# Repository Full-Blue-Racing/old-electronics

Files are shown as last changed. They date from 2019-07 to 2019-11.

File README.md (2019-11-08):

# FBR20-Electronics

This repo houses all the code the car needs to run, separated into steering 
wheel, telemetry, and CAN bus files.

# Git Gud

[Git Crash Course](https://rogerdudler.github.io/git-guide/)

[Gitlab SSH setup](https://docs.gitlab.com/ee/ssh/)

Git can be separated into remote and local repository (repo), how it works is 
that you can *clone* a repo to your local machine, *add* files you would like 
git to track, *commit* your changes to your local branch, *pull* changes by 
others from the remote repo, and *push* your own local changes. Locally git can 
be separated into three areas:

```Untracked files -> tracked files -> staging area```

Untracked files are usually not part of the project and will not be added to the
repo. Tracked files are project files, and files in here will have status shown 
(i.e. new file/changed/renamed...). The staging area is files that are ready to 
be *committed*, and tracked files needs to be added by ```git add```.

These are the only commands I would recommend using on the command line/IDE, 
for more complex commands (such as creating pull requests for merging branches) 
use the web interface. 

![Image of Git Workflow](https://hackernoon.com/hn-images/1*mQdKYVN0nl-NvTw6MOSkWA.png)

# Best Practices

### No spaces in file names or folder names please

**No direct pushing/committing on the master branch**

1. Use branches

Each of the following tasks are on a separate 
branch, please work on the branch relevant to your task. If multiple people are 
on the same branch please make sub-branches from the main task branch 

*e.g.* 
```
steering-wheel -> steering-wheel-warninglights
               -> steering-wheel-RPM-lights
```

We will merge them into the main steering-wheel branch when you make a merge 
request to the task branch.

2. Micro-commit

Commit every time you've implemented a feature - it allows easy rollback to 
previous version without too much code loss if things go wrong (and they *WILL* 
go wrong).

3. Handy commands

```git config --global user.name <display name>``` - sets your name on your commits to the repo

```git clone <path/to/directory>``` - clones a local copy of the repo to your
machine so you can make changes.

```git pull origin <name of branch>``` - pulls any changes others have 
published on the remote branch of the said name since your last update/ initial 
clone

```git add <file to be added>``` - adds file to the staging area to be included 
in the next commit.

```git commit -m "Commit message here"``` - commits file to the local branch 
with the commit message - please make the commit message meaningful so it is 
easier to backtrack (**Not** ```Add new file```) 

```git push origin <name of branch>``` - push your local commits to the remote 
repo on the named branch. Note that on the first push git may require you to 
set the upstream branch with ```git branch --set-upstream-to <name of head branch>```

```git remote update origin --prune``` - updates branches and removes merged branches 
on your local machine.

# Tasks

Each function to be made are described in respective folders' ```README```,
please edit the ```README``` with your name if you are currently working on the 
task, and remove it if not. If someone is already working on one and you want 
to join, contact them and see if you can help before writing your own code. 
Otherwise just write your name down and contact me (Will) for any 
questions/purchasing.

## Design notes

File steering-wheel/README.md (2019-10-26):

# Steering Wheel LEDs: Ashley & Antonis?

On the steering wheel we have rpm LEDs and indicator LEDs, previously
they were fixed colour LEDs and each one had its own pin on the arduino to 
drive it. This year we want to switch to using WS2812B LEDs (you can find a 
better/ alternative solutions, these are just common) They are RGB LEDs that
are controlled by clocking information through them in series. You can buy 
them in a strip for the purposes of developing them into code.
    
[Link to LED Datasheet](https://cdn-shop.adafruit.com/datasheets/WS2812B.pdf)
    
## Function Requirements:
    
1. We want 19 display LEDs in series. The first and last two are for
   warning lights. The central 15 are for rpm lights
   (see [https://www.youtube.com/watch?v=u5kZjg_sJdg])
  
2. Two variables are passed to the function:
    -rpm (float(can be integer) - revs per minute of engine)
    -clt (float - coolant temperature)
    
3. Warning lights (clt value):
    - below 35 C - LEDs solid blue
    - Between 35 C and 100 C - LEDs off
    - between 100C and 107 C - LEDs solid red
    - Above 107 C - LEDs flashing red
    - Values are rough. Do some research to get more accurate
      information and link your sources. Contact me for engine 
      details

4. RPM lights (rpm value):
    - (left to right) 5 Green, 5 Red, 5 Blue
    - Threshold for each to turn on is a design choice you have to make 
      (do some research and produce a document as this scores points in 
      design presentation) Jonathan Collins is one of the best racers
      in Cambridge so speak to him if you want an idea.
    - Above 12500 ALL the LEDs flash blue (note do this via interrupts, 
      never use delays if possible)

# Steering Wheel Screen: (Insert Name 1 & Name 2 & Name 3 here)

previously we used a screen driven directly via an arduino nano. The problem
was that the arduino was 8-Bit so this meant it lacked the speed to update the
screen smoothly enough to do graphics (could only do text).

This means we have switched to using a Nextion screen:
[Link to Nextion Webside](https://nextion.itead.cc/)

These are seperate microprocessor/screen units that operate at 32-bit. Allowing
graphical displays. They work by communicating via serial to an arduino in the 
steering wheel that is pulling data off the CAN bus.

## Functional Requirements:

1. Decide on which Model to use. There are multiple options so take a look
   at each of the different series and document the option you went for. In 
   terms of size to choose, last year we went with a 3.5" screen and I can
   send photos/CAD of that to give you an idea of size relative to the steering
   wheel. We are going to be reusing the same shape of the centre of the
   wheel so a step down to the 3.2" screen is an idea to play with. Best thing
   to do is play around with CAD and see what will fit with the extra LEDs that
   are going to be at the side of the screen (look at an f1 steering wheel)

2. One of the buttons on the steering wheel will be used to toggle through the
   different screen display modes:
    - Driver Mode
    - Data Mode
    - Standby Mode

3. Keep in mind visibility in the sun and the fact the driver is shaken
   around a lot

4. Driver Mode:
    - Contains a central RPM dial similar to that in cars
    - Clear temperature readoff for clt (coolant temp)
    - Keep in mind the steering wheel tilts when turned when designing
      graphics
    - Display showing gear that you are in (bug me to add this to the car)
    - Other parameters may be added

5. Data Mode:
    - Display all the datafields received over CAN bus in a clear format
    - Might need to display over multiple screens but that is fine

6. Standby Mode:
    - Simply display an image on the screen, if possible a GIF or most desirably
      a Video

# Steering Wheel PCB: (Insert name here)

We need to connect all these components together on the steering wheel. This
will require a complex (multi-layer) PCB to connect them together. This will 
require CAD skills as well. 

## Functional requirements (To do):

1. Get a full spec list of everything to connect together:
    - Schematics for connections
    - CAD models of each component

2. Design a multi-layer PCB:
    - Will need to design as seperate projects in KiCad
    - Have to consider layout of LEDs and buttons (need to choose buttons)
    - We want to be able to modify the code on the device so make it possibe to access programming ports/ add external connector
    - Include mounting holes and design how it is supposed to be assembled together

3. Produce an accurate CAD model of each of the parts and an assembly of the whole thing together
    - !!!No incomplete constraints!!!

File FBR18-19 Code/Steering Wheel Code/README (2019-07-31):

This is the code for the steering wheel,

The single_test was for the breadboarded screen and LEDs, this worked in
isolation with the code generating rpm and clt values to be displayed

The other two pieces of code went on two arduinos. One was in the dash and
had the can circuitry, it then extracted the relevant information and sent 
it over a serial link to another arduino in the steering wheel which controlled
the screen and the LEDs. 

We encountered two problems:
-Serial is annoying to get working between two arduinos (basically like
working with an incomplete library). This resulted in the serial communications
interfering with the screen (believed to be due to using the same register to
communicate with each device) so we only ran the RPM LEDs
-The CAN circuitry in the dash was never tested and it never worked, this 
could be due to a multitude of things but the learning point is to test
PCBs you have designed, even if it worked on a breadboard

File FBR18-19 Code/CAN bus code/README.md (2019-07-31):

This is the breakdown of how information is extracted from the CAN messages,
if you are unfamilliar with CAN then the following links are useful:

Good get up to speed video:
-https://www.youtube.com/watch?v=FqLDpHsxvf8

A lot of info on how it actually works (not actually necessary to code as this
is all done via library functions and ICs):
-http://www.ti.com/lit/an/sloa101b/sloa101b.pdf

Tutorial used to develop code
-https://www.instructables.com/id/Yes-We-CAN-BUS-With-Arduino-in-30-Seconds/

Documentation on current ECU (Note we use a microsquirt but it has the 
same CAN bus protocol as a megasquirt, also we just use the simplified dash 
broadcasting as the additional information omitted is still received over a 
physical serial connection to a laptop running TunerStudio MS but it is not
needed at all when on track)
-http://www.msextra.com/doc/pdf/Megasquirt_CAN_Broadcast.pdf

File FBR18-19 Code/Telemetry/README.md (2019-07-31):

https://howtomechatronics.com/tutorials/arduino/arduino-wireless-communication-nrf24l01-tutorial/

This is a tutorial on using the NRF24l01 radio modules to transmit data,

These have been tested roughly and are suitable for the distances we want to use
but they have not been tested with the engine running (emf noise might be 
significant)

All this code has been tested and works in pulling data off the CAN bus
and transmitting and receiving it. Currently we use the software 
TelemetryViewer_v0.4 to plot it which is open source, link to the creator:
http://www.farrellf.com/TelemetryViewer/
(There is a newer version which would be good to familiarise yourself with.
 The old one had a bug where an error came up, if you kept spamming ok it
 just worked)

Might be worth doing research on other radio modules/solutions that we can use
before you begin coding but if possible use these as they are very cheap 
(will require extensive testing first though - hint to get them to work is
to encase the electronics is a faraday shield)

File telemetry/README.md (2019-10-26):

# Telemetry Software: (INSERT NAME HERE)

If you want to develop software that plots data in real-time in several
different graph types message then I will make a detailed plan but it's
the most difficult task. It is beyong my coding skills/understanding
so you will be on your own. We have something that does this already so
no-one feel obliged to work on it.

# Post race analysis: (INSERT NAME HERE)

You will be given a .csv file containing all the data for a test session.
You need to write some code that will plot all this data in meaningful plots.
The best form for this to be in is an interactive tool that works with the
following steps:
1. Select number of graphs to plot
2. Select time range to consider (universal)
3. Select graph type for each
4. Select data fields for each graph
5. Display graphs

## To Do:

1. Get a list of all the data-fields you need to plot. As a base, consult the ECU documentation on Nuclino to see what is gauranteed:
    - Note you need to code this in a way so that additional data-fields are easily added

2. Determine the types of graphs we are interested in. A few examples are:
    - Data against time (e.g. rpm vs time)
    - Data against data (e.g. coordinates of car)
    - Histogram graphs
    - Fast fourier transform

3. Implement the solution in code to perform the above. Some useful features:
    - Add thresholds to data-fields that flags up when data exceeds them, e.g. colour of line you are plotting changes
    - Cursor functionality to read off values from graphs
    - Cursor on one graph also shows the corresponding data-point on other graphs

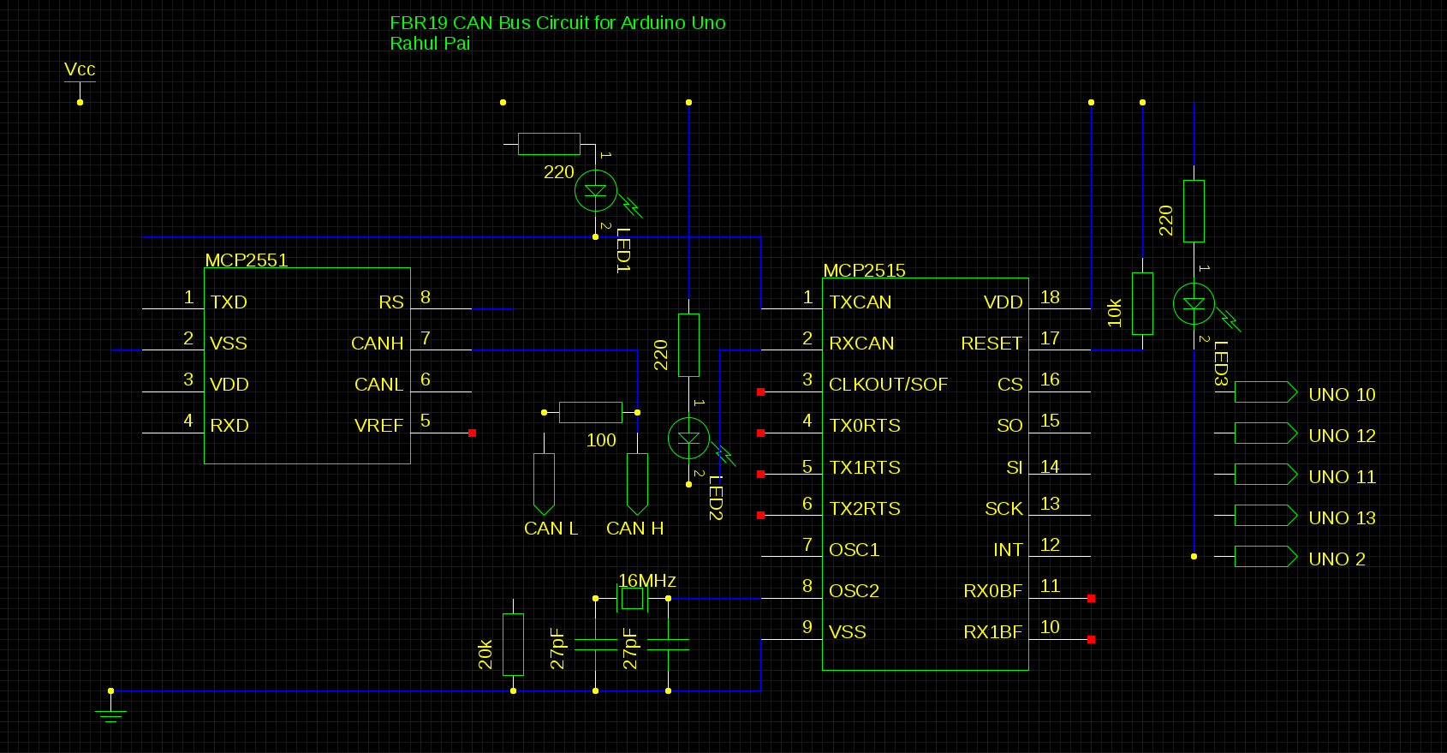
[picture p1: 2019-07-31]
FBR18-19 Code/CAN bus code/Circuit_Diagram.png

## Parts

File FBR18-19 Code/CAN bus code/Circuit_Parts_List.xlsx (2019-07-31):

CAN Bus Decode Circuit For Arduino
 | Part | Quanity | unit price | total price | notes | link
 | 16MHz Crystal | 1 | £0.36 | £0.36 |  | https://uk.farnell.com/txc/9b-16-000maaj-b/xtal-16-000mhz-18pf-hc-49s/dp/1842216
 | MCP2515-I/P | 1 | £1.42 | £1.42 |  | https://uk.farnell.com/microchip/mcp2515-i-p/controller-can-spi-pdip18-2515/dp/1439391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
 | MCP2551-I/P | 1 | £0.83 | £0.83 |  | https://uk.farnell.com/microchip/mcp2551-i-p/ic-can-transceiver-dip8-2551/dp/1292240
 | Red LED | 5 | £0.28 | £1.40 | min 5 | https://uk.farnell.com/broadcom-limited/hlmp-1340/led-3mm-red-55mcd-626nm/dp/1003201?st=LED
 | 220 Ohm | 10 | £0.02 | £0.21 | min 10 | https://uk.farnell.com/multicomp/mcf-0-25w-220r/res-220r-5-250mw-axial-carbon/dp/9339299?st=220%20ohm
 | 100 Ohm | 10 | £0.02 | £0.20 | min 10 | https://uk.farnell.com/multicomp/mcf-0-25w-100r/res-100r-5-250mw-axial-carbon/dp/9339043
 | 10k Ohm | 10 | £0.02 | £0.18 | min 10 | https://uk.farnell.com/multicomp/mcre000049/res-10k-5-125mw-axial-carbon-film/dp/1700251
 | 20k Ohm | 10 | £0.03 | £0.29 | min 10 | https://uk.farnell.com/multicomp/mf12-20k/res-20k-1-125mw-axial-metal-film/dp/9342796
 | 27pF | 5 | £0.39 | £1.97 | min 5 | https://uk.farnell.com/kemet/c317c270j5g5ta7301/cap-27pf-50v-5-c0g-np0/dp/2575647
 | Total |  |  | £6.86

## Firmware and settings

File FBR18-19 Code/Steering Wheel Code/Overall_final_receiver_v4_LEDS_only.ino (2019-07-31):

/***************************************************
  This is our library for the Adafruit HX8357D Breakout
  ----> http://www.adafruit.com/products/2050

  Check out the links above for our tutorials and wiring diagrams
  These displays use SPI to communicate, 4 or 5 pins are required to
  interface (RST is optional)
  Adafruit invests time and resources providing this open source code,
  please support Adafruit and open-source hardware by purchasing
  products from Adafruit!

  Written by Limor Fried/Ladyada for Adafruit Industries.
  MIT license, all text above must be included in any redistribution
 ****************************************************/

// Cannot serial print on this as this massively ruins/ effects the received data

#include <SPI.h>
#include "Adafruit_GFX.h"
#include "Adafruit_HX8357.h"
#include <math.h>

// These are 'flexible' lines that can be changed
#define TFT_CS 10
#define TFT_DC 9
#define TFT_RST -1 // RST can be set to -1 if you tie it to Arduino's reset

// Use hardware SPI (on Uno & Nano, #13, #12, #11) and the above for CS/DC
Adafruit_HX8357 tft = Adafruit_HX8357(TFT_CS, TFT_DC, TFT_RST);

// SoftSPI - note that on some processors this might be *faster* than hardware SPI!
//Adafruit_HX8357 tft = Adafruit_HX8357(TFT_CS, TFT_DC, MOSI, SCK, TFT_RST, MISO);

int rpm = 0;
int rpm_temp;         // Temp values are used for input checks
int clt;
int clt_temp;
int skips = 0;        // Used to set how many times RPM updates before CLT does
int screen_state = 0; // 0 = black background, 1 = red background
int flash = 0;        // Used to detect when set blue is called the first time 


// LED assignments
const int LED_G_1 = A5;
const int LED_G_2 = A4;
const int LED_G_3 = A3;
const int LED_G_4 = A2;
const int LED_R_5 = A1;
const int LED_R_6 = A0;
const int LED_R_7 = 2;
const int LED_R_8 = 3;
const int LED_R_9 = 4;
const int LED_B_10 = 5;
const int LED_B_11 = 6;
const int LED_B_12 = 7;
const int LED_B_13 = 8;

// Button assignments
const int button_L = A6;

const byte numChars = 32;
char receivedChars[numChars];
char tempChars[numChars];        // temporary array for use when parsing

      // variables to hold the parsed data
char messageFromPC[numChars] = {0};
int integer1FromPC = 0;
int integer2FromPC = 0;

boolean newData = false;

 // USed for flashing
const long interval = 150;           // interval at which to blink (milliseconds)
unsigned long previousMillis = 0;        // will store last time LED was updated

void setup() {
  Serial.begin(9600);
  tft.begin();

  // read diagnostics (optional but can help debug problems)
  uint8_t x = tft.readcommand8(HX8357_RDPOWMODE);

  tft.setRotation(1);                            // Setting orientation of screen
  tft.setTextColor(HX8357_WHITE, HX8357_BLACK);  // Setting the text colour
  set_black();

  // Setting up each of the pins as LED outputs
  pinMode(LED_G_1, OUTPUT);
  pinMode(LED_G_2, OUTPUT);
  pinMode(LED_G_3, OUTPUT);
  pinMode(LED_G_4, OUTPUT);
  pinMode(LED_R_5, OUTPUT);
  pinMode(LED_R_6, OUTPUT);
  pinMode(LED_R_7, OUTPUT);
  pinMode(LED_R_8, OUTPUT);
  pinMode(LED_R_9, OUTPUT);
  pinMode(LED_B_10, OUTPUT);
  pinMode(LED_B_11, OUTPUT);
  pinMode(LED_B_12, OUTPUT);
  pinMode(LED_B_13, OUTPUT);

  // Setting up the buttons
  pinMode(button_L, INPUT_PULLUP);
}


void loop(void) {
    recvWithStartEndMarkers();
    if (newData == true) {
        strcpy(tempChars, receivedChars);
            // this temporary copy is necessary to protect the original data
            //   because strtok() used in parseData() replaces the commas with \0
        parseData();
        showParsedData();
        newData = false;
    }
      

    if (clt > 107)            // This is the high alert warning threshold
    {
      screen_state = 1;
      set_black();
      set_red();
    }
    else if (clt > 100)       // This is the caution threshold
    {
      if (screen_state != 1)
      {
        set_red();
      }
      screen_state = 1;
    }
    else
    {
      if (screen_state != 0)
      {
        set_black();
      }
      screen_state = 0;
    }
    


    // LED light up section
    if (rpm < 12500)
    {
      if (rpm > 600)
      {
        digitalWrite(LED_G_1, HIGH);
      }
      else
      {
        digitalWrite(LED_G_1, LOW);
      }
      if (rpm > 600)
      {
        digitalWrite(LED_G_2, HIGH);
      }
      else
      {
        digitalWrite(LED_G_2, LOW);
      }
      if (rpm > 1900)
      {
        digitalWrite(LED_G_3, HIGH);
      }
      else
      {
        digitalWrite(LED_G_3, LOW);
      }
      if (rpm > 3200)
      {
        digitalWrite(LED_G_4, HIGH);
      }
      else
      {
        digitalWrite(LED_G_4, LOW);
      }
      if (rpm > 4500)
      {
        digitalWrite(LED_R_5, HIGH);
      }
      else
      {
        digitalWrite(LED_R_5, LOW);
      }
      if (rpm > 5800)
      {
        digitalWrite(LED_R_6, HIGH);
      }
      else
      {
        digitalWrite(LED_R_6, LOW);
      }
      if (rpm > 7100)
      {
        digitalWrite(LED_R_7, HIGH);
      }
      else
      {
        digitalWrite(LED_R_7, LOW);
      }
      if (rpm > 8400)
      {
        digitalWrite(LED_R_8, HIGH);
      }
      else
      {
        digitalWrite(LED_R_8, LOW);
      }   
      if ((rpm > 9700) & (rpm <= 12500))
      {
        digitalWrite(LED_R_9, HIGH);
      }
      else
      {
        digitalWrite(LED_R_9, LOW);
      } 
      if (rpm > 11000)
      {
        digitalWrite(LED_B_10, HIGH);
      }
      else
      {
        digitalWrite(LED_B_10, LOW);
      } 
      if (rpm > 12000)
      {
        digitalWrite(LED_B_11, HIGH);
      }
      else
      {
        digitalWrite(LED_B_11, LOW);
      }
      digitalWrite(LED_B_12, LOW);
      digitalWrite(LED_B_13, LOW);  
      flash = 0;    
    }
    else
    {
      set_blue();
    }
}


//============

void recvWithStartEndMarkers() {
    static boolean recvInProgress = false;
    static byte ndx = 0;
    char startMarker = '<';
    char endMarker = '>';
    char rc;

    while (Serial.available() > 0 && newData == false) {
        rc = Serial.read();

        if (recvInProgress == true) {
            if (rc != endMarker) {
                receivedChars[ndx] = rc;
                ndx++;
                if (ndx >= numChars) {
                    ndx = numChars - 1;
                }
            }
            else {
                receivedChars[ndx] = '\0'; // terminate the string
                recvInProgress = false;
                ndx = 0;
                newData = true;
            }
        }

        else if (rc == startMarker) {
            recvInProgress = true;
        }
    }
}

//============

void parseData() {      // split the data into its parts

    char * strtokIndx; // this is used by strtok() as an index

    strtokIndx = strtok(tempChars,",");      // get the first part - the string
    rpm_temp = atoi(strtokIndx);     // convert this part to an integer
    strtokIndx = strtok(NULL, ",");
    clt_temp = atof(strtokIndx);     // convert this part to an integer
    if (((rpm_temp > 200) & (rpm_temp <= 20000)) & ((clt_temp > 0) & (clt_temp <= 200)))
    {
      rpm = rpm_temp;
      clt = clt_temp;
    }
}

//============

void showParsedData() {
    // Displaying RPM
    /*
    tft.setCursor(60, 50);     // Commented out because this corrupts? the serial data being sent
    tft.print(rpm);
    tft.print("  ");

    // Displaying CLT

    if (skips == 10)          // This controls the ratio at which rpm is updated relative to clt,
    {                         // Meaning the relative refresh rate is rpm:clt = skips:1
      tft.setCursor(120, 200);
      tft.print(clt);
      tft.print(" "); 
      skips = 0;  
    }
    skips += 1; */
}


unsigned long set_black(){
  tft.fillScreen(HX8357_BLACK);                  // Setting the background colour
}

unsigned long set_blue(){
  // The code to flash LEDs goes here, this doesnt affect the screen at all
  if (flash == 0)
  {
    digitalWrite(LED_G_1, HIGH);
    digitalWrite(LED_G_2, HIGH);
    digitalWrite(LED_G_3, HIGH);
    digitalWrite(LED_G_4, HIGH);
    
    digitalWrite(LED_R_5, HIGH);
    digitalWrite(LED_R_6, HIGH);
    digitalWrite(LED_R_7, HIGH);
    digitalWrite(LED_R_8, HIGH);
    digitalWrite(LED_R_9, HIGH);
    
    digitalWrite(LED_B_10, HIGH);
    digitalWrite(LED_B_11, HIGH);
    digitalWrite(LED_B_12, HIGH);
    digitalWrite(LED_B_13, HIGH);  
    flash = 1;  
  }
  
  unsigned long currentMillis = millis();
  if (currentMillis - previousMillis >= interval) {
    // save the last time you blinked the LED
    previousMillis = currentMillis;

    // if the LEDs are off turn it on and vice-versa:
    digitalWrite(LED_G_1, !digitalRead(LED_G_1));
    digitalWrite(LED_G_2, !digitalRead(LED_G_2));
    digitalWrite(LED_G_3, !digitalRead(LED_G_3));
    digitalWrite(LED_G_4, !digitalRead(LED_G_4));
    
    digitalWrite(LED_R_5, !digitalRead(LED_R_5));
    digitalWrite(LED_R_6, !digitalRead(LED_R_6));
    digitalWrite(LED_R_7, !digitalRead(LED_R_7));
    digitalWrite(LED_R_8, !digitalRead(LED_R_8));
    digitalWrite(LED_R_9, !digitalRead(LED_R_9));
    
    digitalWrite(LED_B_10, !digitalRead(LED_B_10));
    digitalWrite(LED_B_11, !digitalRead(LED_B_11));
    digitalWrite(LED_B_12, !digitalRead(LED_B_12));
    digitalWrite(LED_B_13, !digitalRead(LED_B_13));
  }
}

unsigned long set_red(){
  tft.fillScreen(HX8357_RED);                  // Setting the background colour

  tft.setTextSize(8);

  tft.setCursor(120, 100);
  tft.print(clt);
}

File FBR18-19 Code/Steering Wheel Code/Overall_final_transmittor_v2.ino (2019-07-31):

/**************************
 *         Author         *
 *      omarCartera       *
 *                        *
 *        5/8/2017        *
 *                        *
 * c.omargamal@gmail.com  *
 **************************/

#include <SPI.h>          // SPI is used to talk to the CAN Controller
#include <mcp_can.h>

MCP_CAN CAN(10);          // set SPI Chip Select to pin 10 - this is just the wiring we use, dont change

unsigned char len = 0;    // }
unsigned char buf[8];     //  } These are variables to do with the output of the CAN library functions, buf is a 8 part character in which individual value represents a byte, look at the tutorial website to understand this
unsigned int canID;       // }

int manifold_air_pressure;   // these are the names of all the data that is outputted, see http://www.msextra.com/doc/pdf/Megasquirt_CAN_Broadcast.pdf page 2
int rpm;                     // all the units are linked in the document above
int clt;                     // In the code, unsigned integers are used with the prefix engine (we need these are information arrives in several bits and we can use this data format to modify the data more easily), these are converted to floats before being sent as according to the datasheet they need to be divided so this avoids errors
int tps;                     // This does involve a conversion from unsigned to signed but we dont need to worry about this unless we reach values of 32767 (unlikely)
                             // All of these values need to be divided by a certain value before they can be displayed, this is in the documentation attached and we are going to only do this at the end as it is easier to transmitt integers

char text[32];               // This is used to transmit the data over serial

unsigned int temp;           // This is a temporary variable used to convert the two 8 bit parts of each value to one 16 bit one

void setup()
{
  Serial.begin(9600);   // To communicate with Serial monitor, lower this if stability issues?
  // Tries to initialize the CAN bus reader, if failed --> it will loop here for ever
  START_INIT:
  
      if(CAN_OK == CAN.begin(CAN_500KBPS))      //setting CAN baud rate to 500Kbps - dont change as microsquirt uses this baud rate
      {
          Serial.println("CAN BUS Shield init ok!");
      }
      else
      {
          Serial.println("CAN BUS Shield init fail");
          Serial.println("Init CAN BUS Shield again");
          delay(100);
          goto START_INIT;
      }
}



void loop()
{
    if(CAN_MSGAVAIL == CAN.checkReceive())    // Check if data is coming - if having problems look at previous versions for printing statements
    {
        CAN.readMsgBuf(&len, buf);    // Read data,  len: data length, buf: data buffer
        canID = CAN.getCanId();       // Getting the ID of the incoming message - note ensure that the microquirt is outputting in the simplified dashboard mode which is set in tuner studio

        if (canID == 1512)            // Manifold air pressure, Engine RPM, Coolant temperature and Throttle position datafields, we arent interested in the others
        {                
          // Engine RPM  
          unsigned int engine_rpm = buf[2];
          engine_rpm = engine_rpm << 8;
          temp = buf[3];
          engine_rpm = engine_rpm + temp;         
          rpm = engine_rpm;               

          // Coolant Temperature
          unsigned int engine_clt = buf[4];
          engine_clt = engine_clt << 8;
          temp = buf[5];
          engine_clt = engine_clt + temp;
          clt = engine_clt;
          clt = (clt - 320) * 5 / 90;  

          // Note these sent values are integers and still need to be scaled and have their units converted
        }
  snprintf(text, 32, "<%d,%d>", rpm, clt);
  Serial.println(text);
    }
}

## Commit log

2019-07-31 This code is the basis used to read data from the CAN bus
2019-07-31 Schematic used for anyone interested
2019-07-31 Parts list
    [Circuit_Parts_List.xlsx]
2019-07-31 Transmitter code, note this reads data off the CAN bus so only a few lines in the beginning and setup and the last three are relevant
2019-08-01 New directory to contain the 2019-20 steering wheel code
2019-08-01 Directory for the new CAN bus code
2019-08-01 This is the the overall "master" code for the steering wheel which will be uploaded to the final thing. I will be taking your functions and combining them on here so don't worry about adding to it.
2019-08-01 Update README.md to include instructions for the steering wheel indicator LEDs function
2019-08-02 Added README for steering wheel folder
2019-08-03 Update steering wheel README.md to include the screen microprocessor part of the steering wheel code
2019-08-09 Tentatively putting name down for Steering Wheel LED task
2019-10-15 Added Antonis to working on the steering wheel LEDs
2019-10-26 Update README.md for 3 people to work on the steering wheel screen. Also adding one section for the steering wheel PCB design.
2022-10-10 Added block diagram of loom
    [CLT.kicad_sch, Dash Arduino.kicad_sch, Dash switches.kicad_sch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]
2022-10-10 Starter and fusebox change
    [Loom.kicad_sch]
2022-10-16 Added detailed version of schematic
    [BSPD.kicad_sch, CLT.kicad_sch, ECU.kicad_sch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]
2022-10-30 Added fuel pump, TPS(BSPD), BPS.
    [BPS.kicad_sch, Lambda.kicad_sch, Loom23_detailed.kicad_sch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]
2022-10-31 Added dash switches and crank sensor.
    [Dash switches.kicad_sch, Loom23_detailed.kicad_sch, crankSensor.kicad_sch]
2022-11-06 Added fans and their control circuit. Added some wires.
    [CamSensor.kicad_sch, CoolingFan.kicad_sch, Dash switches.kicad_sch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]
2022-11-07 Finished wiring up the ECU.
    [Dash switches.kicad_sch, Lambda.kicad_sch, Loom23_detailed.kicad_sch]
2022-11-13 Added dash/wheel connections
    [Dash Arduino.kicad_sch, DashBoB.kicad_sch, Loom23_detailed.kicad_sch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]
2022-11-13 Removed ride height sensor
    [Loom23_detailed.kicad_sch]
2022-11-13 Included BSPD and started adding labels
    [BSPD.kicad_sch, CoolingFan.kicad_sch, Dash Arduino.kicad_sch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]
2022-11-19 More labels
    [BSPD.kicad_sch, CoolingFan.kicad_sch, Dash Arduino.kicad_sch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]
2022-11-19 Finished wire labels
    [DashBoB.kicad_sch, Loom23_detailed.kicad_sch]
2022-11-20 Created a spreadsheet with all the wires
    [Loom23_detailed.kicad_sch, Loomwires.xlsx]
2022-11-20 Added engine speed sensor, fixed INJ and IGN connections
    [EngineSpeed.kicad_sch, Loom23_detailed.kicad_sch, Loomwires.xlsx]
2022-11-21 Added current ratings
    [Fusebox.kicad_sch, Loom23_detailed.kicad_sch, Loomwires.xlsx]
2022-11-27 Added temp reqs and fuse values
    [Fusebox.kicad_sch, Loom23_detailed.kicad_sch, Loomwires.xlsx]
2023-01-18 Added colours
    [Loom23_detailed.kicad_sch, Loomwires.xlsx]
2023-01-22 Added paddle shifter PCB and the relays.
    [CAN.kicad_sch, Dash Arduino.kicad_sch, DashBoB.kicad_sch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]
2023-02-05 Added brake light
    [DashBoB.kicad_sch, Loom23_detailed.kicad_sch, Loomwires.xlsx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]
2023-02-12 Update Loomwires.xlsx
    Changed some labels to match existing ones.
    [Loomwires.xlsx]
2023-02-13 Changed labels to match in schematic and spreadsheet
    [Loom23_detailed.kicad_sch, Loomwires.xlsx]
2023-02-26 Changes made to fusebox, relayboard and camsensor
    [CamSensor.kicad_sch, Fusebox.kicad_sch, Loom23_detailed.kicad_sch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]
2023-05-16 Changed labels to match old wires
    [Dash switches.kicad_sch, DashBoB.kicad_sch, Fusebox.kicad_sch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]
2023-07-03 Added connector pinouts
    [Dash switches.kicad_sch, Fusebox.kicad_sch, Loom.kicad_sch]
